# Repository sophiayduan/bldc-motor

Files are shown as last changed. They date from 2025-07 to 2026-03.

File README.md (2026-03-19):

# BLDC Motor v2.0

A mostly 3D printed outrunner brushless DC motor with 9 slots and 12 poles, wound in a ~~delta~~ star configuration.



> better photos coming soon

If I wanted the most RPM or torque I would've bought a bldc, this is just a model for fun and to learn from. I'll be using it to test a driver board that I'm currently designing.

Features:
- N52 magnets
- Press fit 3d printed parts
- Removeable base
- Screw holes for mounting
- 3.5mm male banana plugs
- HT-PLA stator





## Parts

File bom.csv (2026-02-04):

Item | Description | Quantity or MOQ | Cost (USD) shipping excluded | Comment | Link
3D printed part | Rotor, stator and base | 3 | 0 | Will print these myself
Ball Bearings | 5x10x4mm | 5 | 2.16 |  | https://www.aliexpress.com/item/1005009062156404.html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
Shaft | 45x5mm | 1 | 1.19 |  | https://www.aliexpress.com/item/1005004018253437.html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
Threaded insert | M2 | 1 | 0 | Already have
Set screw | M2 3mm | 10 | 0.77 |  | https://www.aliexpress.com/item/1005007049952459.html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
Copper wire | 0.5mm 10m | 2 | 6.26 |  | https://www.aliexpress.com/item/1005003799096513.html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
Magnets | N52 20x6x2mm | 20 | 3.64 |  | https://www.aliexpress.com/item/1005009598279358.html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
Shipping |  |  | 12
Total: 26.02 USD

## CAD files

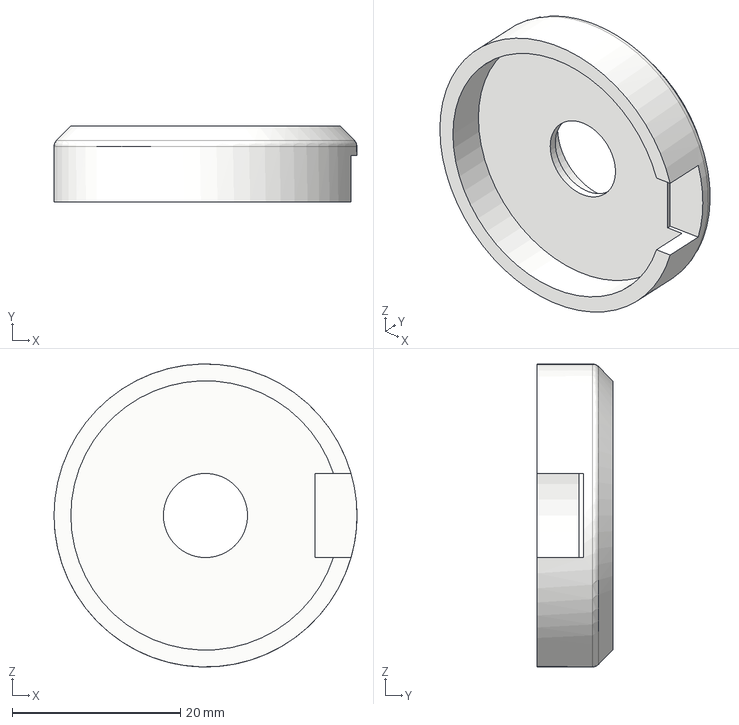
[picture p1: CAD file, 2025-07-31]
to print/base_main.step
36.0 x 9.00 x 36.0 mm

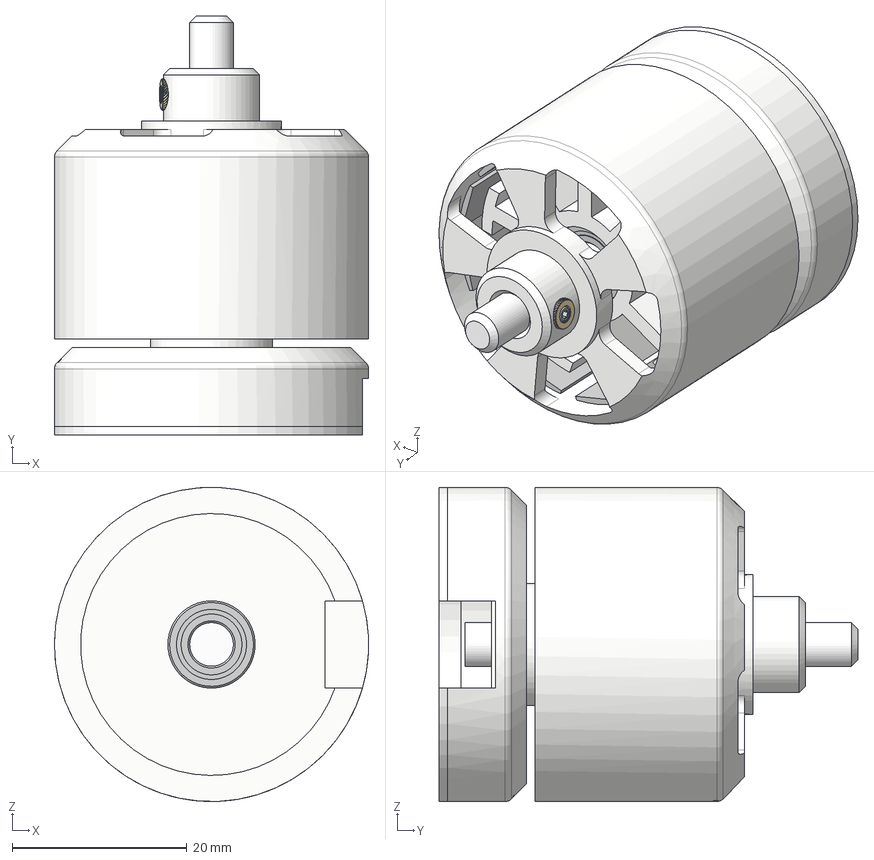
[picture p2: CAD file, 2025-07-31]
motor.step
36.0 x 48.0 x 36.0 mm
94459A767_Heat-Set Inserts for Plastic
92605A042_Stainless Steel Flat-Tip Set Screw
7804K106_Stainless Steel Ball Bearing x 2

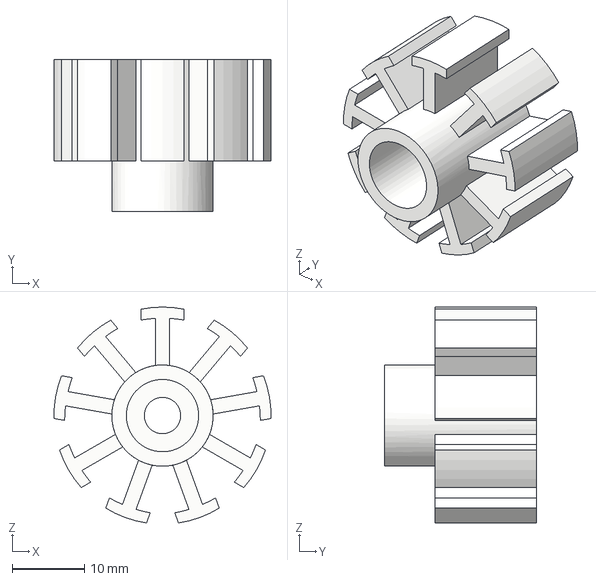
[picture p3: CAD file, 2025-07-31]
to print/stator.step
30.0 x 21.0 x 29.8 mm

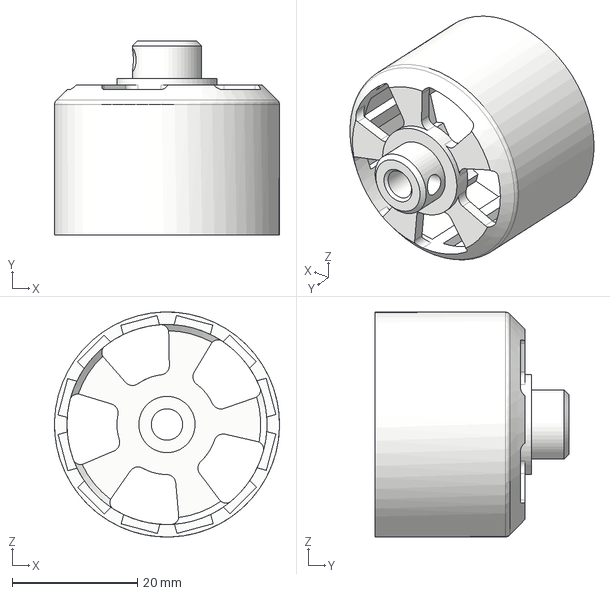
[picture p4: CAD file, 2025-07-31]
to print/rotor.step
36.0 x 31.0 x 36.0 mm

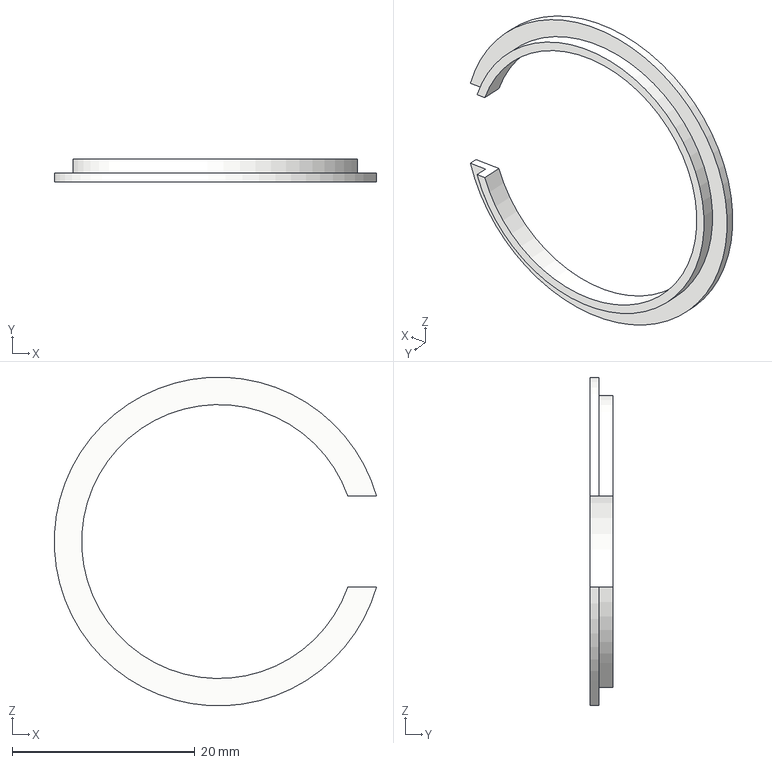
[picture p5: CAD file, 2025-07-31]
to print/base.step
35.3 x 2.50 x 36.0 mm

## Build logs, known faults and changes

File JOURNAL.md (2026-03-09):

---
title: "A BLDC"
author: "Sophia"
description: "A brushless dc motor"
created: "2025-06-13"
---

Total time: 6.5h

# July 30th: Quick project

**Total time spent: 0.5h**

Planning: 
I'll be using 9 slots / 16 poles, it'll be a pain to wind by hand but I'm trying to have decent torque and rpm at the same time.
The shaft will be held by a set screw, and all the 3D printed parts will be press fit.


I also referenced my first 3d printed bldc, it had many many flaws I hope to fix with this design:
- Non existant pressfit
- Shaft is held by friction
- Large for no reason
- Poor CAD
- Circular magnets

# July 31st: Finished
**Total time spent: 6h**
I ended up switching to 9 slots/ 12 poles for a more convential ratio.

Today I finished CADing the entire project, using M2 threaded insert (same as my other project) and some small ball bearings. 

The hardest part was getting the correct dimensions for my stator teeth and rotor, I need to optimize the gap between the magnets, the rotor/stator air gap, keeping the stator teeth reasonable for me to wind by hand and that parts I could find on aliexpress. 

I think I managed to fix all the issues I wanted to tackle with this design.



# Feb 4th: V2.1 Finished
**Total time spent: TOO much**

(Writing this in retrospect) My Aliexpress parts arrived in Sept/Oct, but I didn't have the time to assemble the motor. Or so I thought, I ended up picking this project back up for a school project, and a lot more iterating was done. 

Key changes/additions:
- No more set screw & threaded insert & d-shaft combo, as friction turned out to be more that strong enough
- Used enameled copper wire, originally I had planned (and bought) just regular copper wire
- Powered by a DIY power supply borrowed from my neighbour (had to do some more soldering for this, as originally I was just planning to use a 2-3S LiPo)
- Using a Delta winding configuration (bad idea)
- Simplified parts for 3D printing (less supports needed)
- Added openings on the base, so the wires can actually go through!!
- Used an ESP32 + pot for a servo tester
- Screw holes for mounting
- 3.5mm male banana plugs

This motor did end up spinning, but due to the heat produced by the coils (which was augmented by the delta config), the PLA printed stator started to warp (and melt a bit). This was a huge thing that I missed earlier on, PLA can only go up to 60C approx.

For the next (and likely final) version, i'll swap to Nylon or another high temp filament for the stator, wind it in a Wye (Star) config, and hopefully drive it using a driver board that I design.

# Feb 21st: V2.2 Finished
**Total time spent: too much time.**

- Reprinted the stator with HT-PLA, and then rewound it in a Wye configuration
- Had so many issues with the ESC, espicially the calibration. Looking back, I recongnize that my PSU wasn't providing enough current (along with a multitude of other issues that I fixed)
- Got the motor running consistently! (video in the readme) --Somewhat, the highest current PSU I have access to is _barely_ enough. Otherwise, it works great.

I ended up creating a [tachometer](https://github.com/sophiayduan/tachometer) to measure the RPM of this motor. (I want to determine its kV and efficiency)

It has a nice dashboard, but I'm still working on making the calculated RPM more accurate. 

Got my hands on a ESC (though I'm designing my own rn)

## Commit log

2025-07-31 add .step
    [base.step, base_main.step, motor.step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]
2025-07-31 add bom
    [bom.csv]
2026-02-04 Revise motor description and future plans
    Updated motor configuration and clarified future use.
2026-02-04 remove BOM from readme
2026-02-04 Update BOM
    [bom.csv]
